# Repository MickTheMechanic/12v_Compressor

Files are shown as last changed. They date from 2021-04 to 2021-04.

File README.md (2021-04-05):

# 12v_Compressor

## An open-source Arduino controlled 12v mobile compressor using 3d printed and upcycled parts.

<br />This work is licensed under a <a rel="license" href="http://creativecommons.org/licenses/by-nc/4.0/">Creative Commons Attribution-NonCommercial 4.0 International License</a>.
#

[vid](https://youtube.com/playlist?list=PLsk74wXEuKOpL2YGHRVS3v7fIHzCto8o0)

#

## Overview

The compressor is made up of a used BMW air suspension compressor (manufacturer is WABCO, the same part is also used be Mercedes), some empty 0.95l oxygen tanks (those used for small oxy-acetylene torches), an arduino, and diverse electrical components.

The compressor is controlled via an Arduino Uno, which switches a relay on or off depending on the pressure inside the tanks. The current pressure is displayed on a 2.8" TFT screen. A small lithium battery is included, so that a pressure read out can be achieved without 12v power supply.

- If 12v supply is not present, the power button can be pressed and the display will show a realtime pressure readout for 20 seconds and switch off automatically.
- If 12v supply is present and device is switched off the lithium battery will be recharged
- If 12v supply is present and device is switchen on, the compressor will be powered on and off via the relay automatically depending on realtime pressure. The lithium battery will also be recharged. Realtime pressure will be displayed on screen.

### There are also two status LED's
#### Left LED:
- Red = lithium battery is recharging
- Blue = Lithium battery is fully charged
#### Right LED:
- Green = Tanks are full (if 12v is present relay = off)
- Red = Tanks should be refilled (if 12v is present relay = on)

#
<a href="https://ibb.co/Dz1jNbD">C740-E988-A85-A-4125-8306-F7122-EC01628</a>
#
<a href="https://ibb.co/rd78Jnq">0-F9-DC07-B-1-AC6-40-D4-9-CB7-EE59770-C8-E80</a>
#

#

#

### Extra info

This project relies on a modified version of the GUISlice library. This has been included in the repo

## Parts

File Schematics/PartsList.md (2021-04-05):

1x Arduino Uno
#
1x 2.8" lcd tft display shield
#
1x AO3401 P-channel MOSFET
#
1x IRF9640 (or similar) P-channel MOSFET
#
3x 1N5819 (or similar) diode
#
1x 1N4007 (or similar) diode
#
3x 2N2222A (or similar) NPN transistor
#
3x 470 ohm resistor
#
1x 220 ohm resistor
#
1x 10 kohm resiostor
#
1x 1A MINI fuse
#
1x Mini buck converter
#
1x 5v step up converter
#
1x TP4056 lithium battery charger module
#
1x 12v relay with built in fuse (30A)
#
2x Bi-Color LED (Common Annode!)

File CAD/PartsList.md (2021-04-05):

8x M6 x 25mm cylindrical head allen key bolts
#
8x M6 SW10 nuts
#
4x M5 x 25mm countersunk allen key bolts
#
3x M10x1 brake pipe T joiners
#
2x m10x1 male to male brake pipe joiners
#
1x 300 PSI 5v pressure transducer (1/8 NPT)
#
2x m10x1 6mm push connect fittings
#
1x 1/8 NPT to 1/4 NPT male to male adaptor
#
1x AF2000-02 air dryer
#
1x Automotive breather air filter
#
3x M6 rubber mount

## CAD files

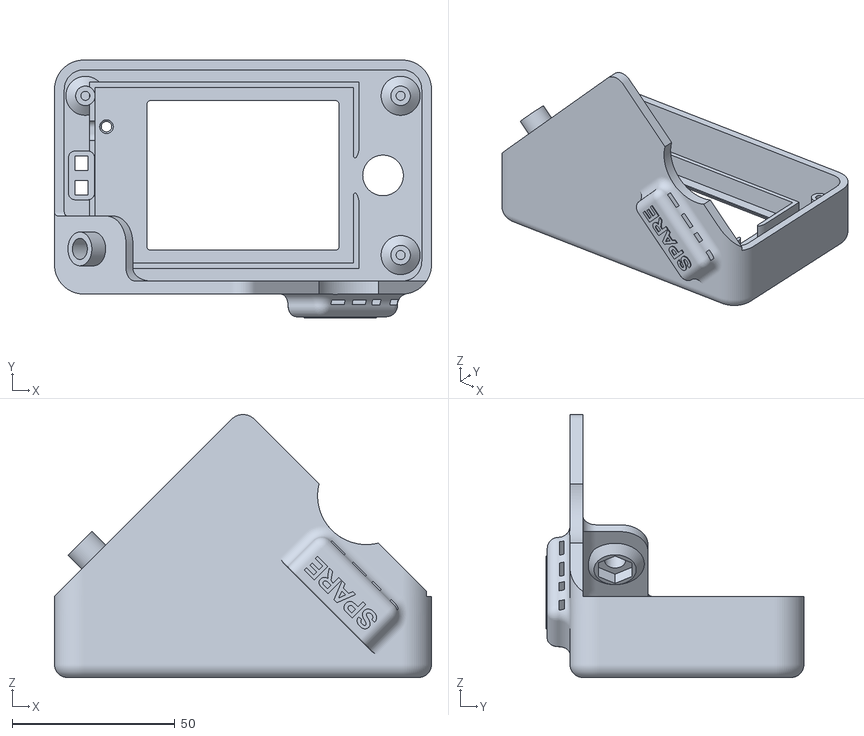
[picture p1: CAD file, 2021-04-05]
CAD/Comp. screen frontV3.stl
116.0 x 79.3 x 80.9

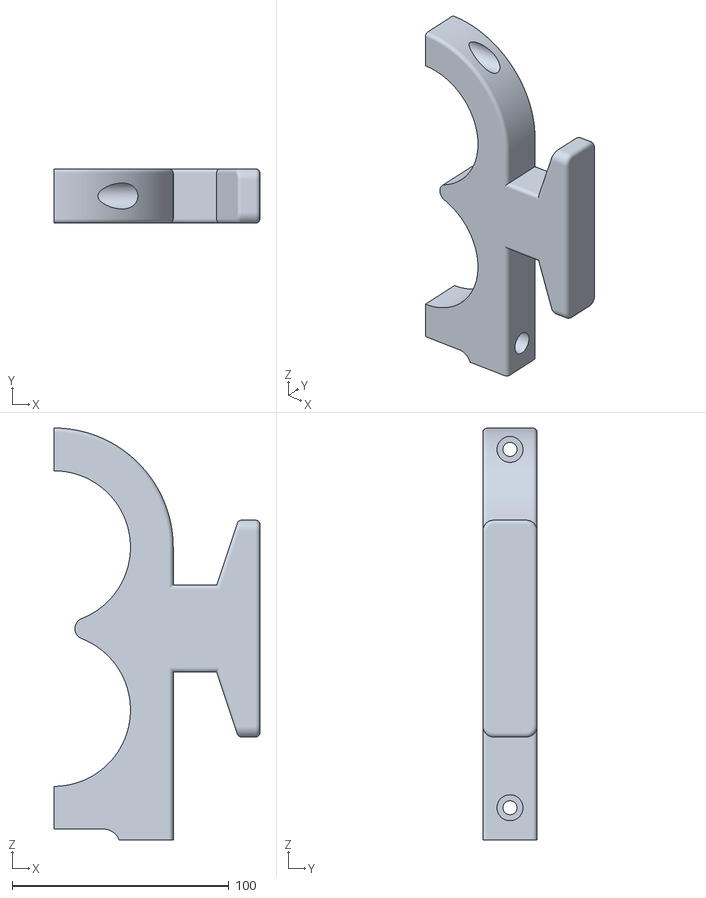
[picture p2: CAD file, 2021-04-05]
CAD/Clamp.stl
95.0 x 25.0 x 190.0

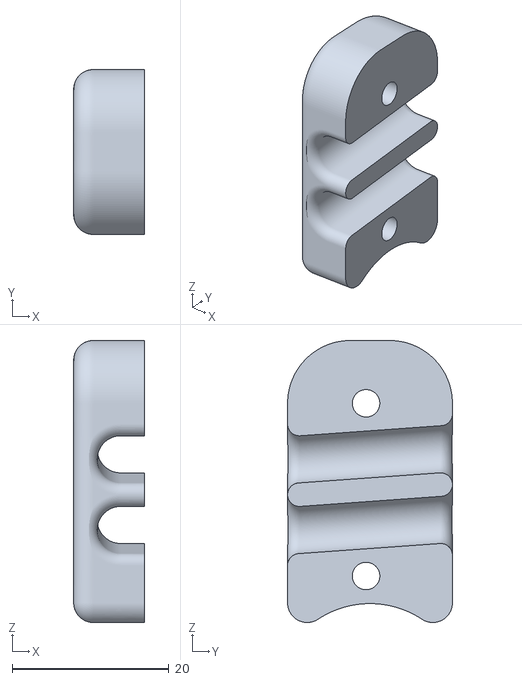
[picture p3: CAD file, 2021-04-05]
CAD/Cable clamp.stl
9.00 x 21.0 x 35.9

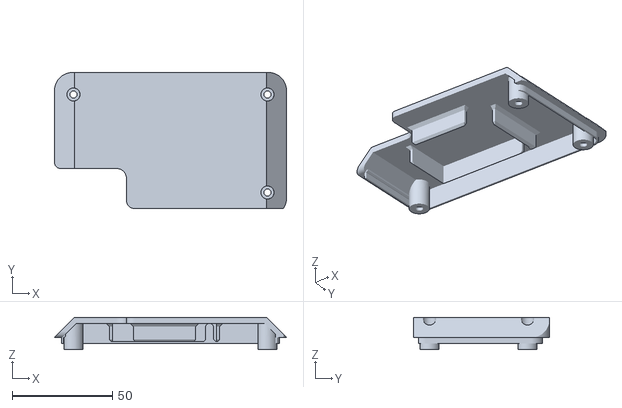
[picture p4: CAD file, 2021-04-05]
CAD/Comp. screen rearV3.stl
116.0 x 68.0 x 16.0

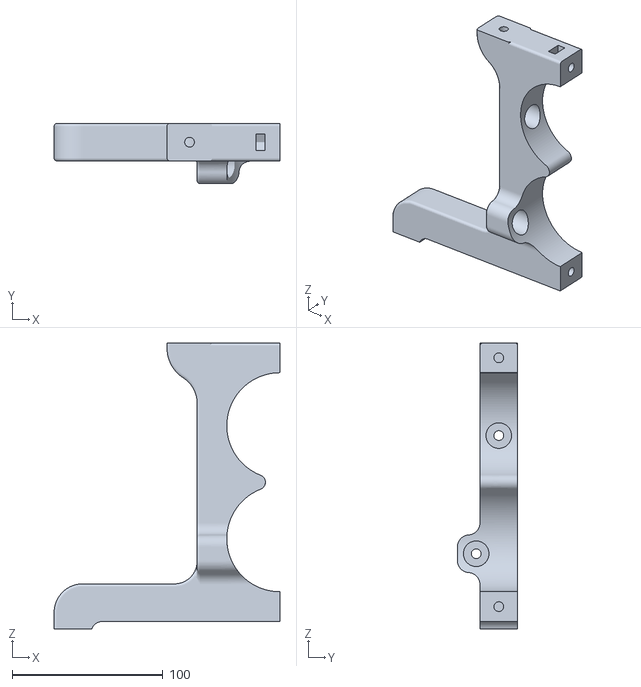
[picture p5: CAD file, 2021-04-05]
CAD/Holder 2.stl
150.0 x 40.0 x 190.0

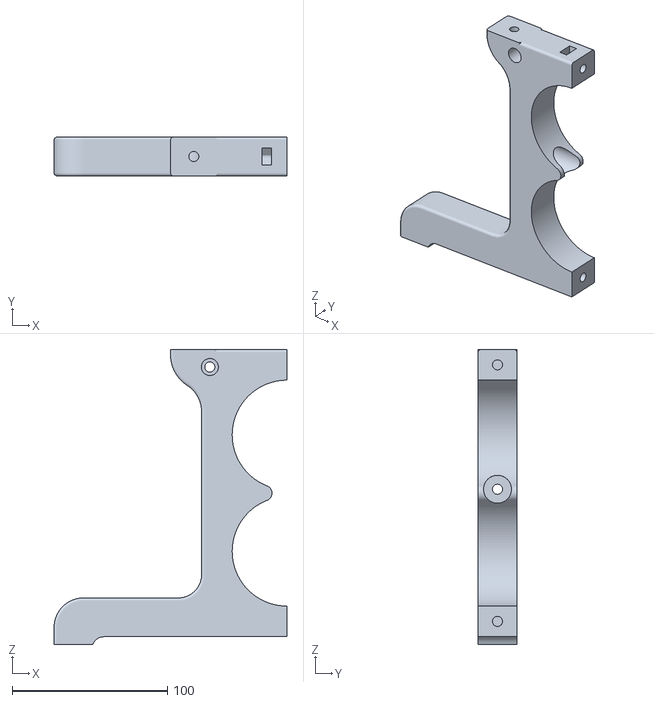
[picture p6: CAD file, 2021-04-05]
CAD/Holder 1.stl
150.0 x 25.0 x 190.0

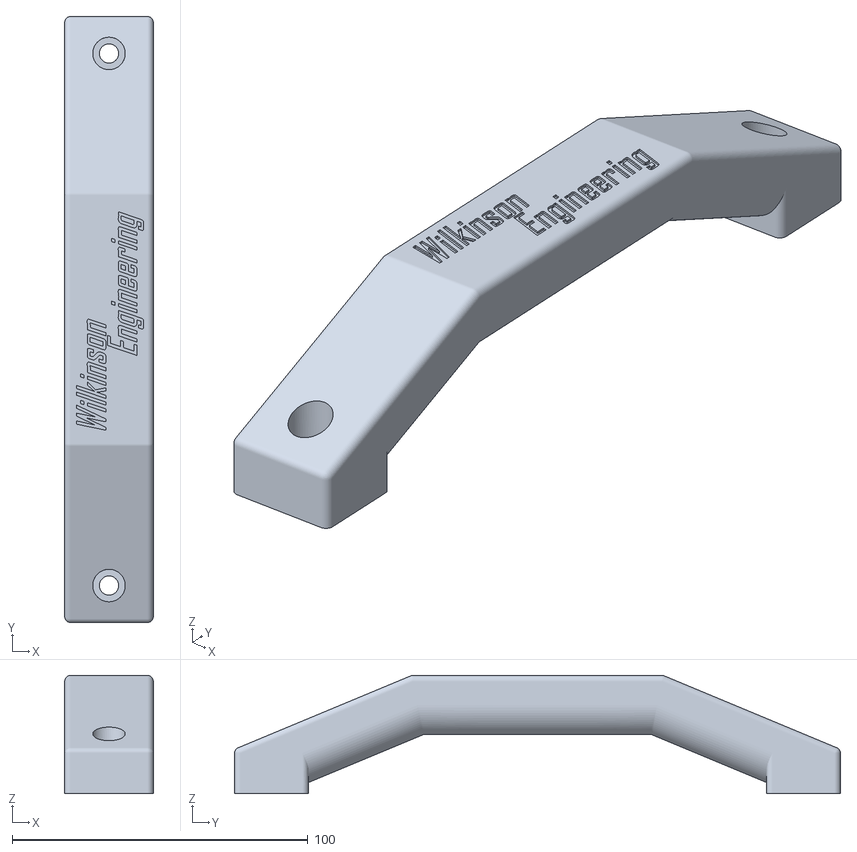
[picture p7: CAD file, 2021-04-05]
CAD/Handle.stl
30.0 x 205.0 x 40.0

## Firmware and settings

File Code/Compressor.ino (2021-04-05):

//Another ridiculously good mod by Mick ;)

#include "GUIslice.h"
#include "GUIslice_drv.h"

// Include any extended elements
#include "elem/XRingGauge.h"

// Defines for resources
#define relayPin 13        //Will turn relay on and off
#define pressurePin A5      //Connected to pressure transducer
#define latchPin  11       //Connected to latch circuit for auto shutdown if display is powered from LiPo and not from 12v
#define buckPin 10


//counting cycles as a makeshift timer. millis and unsigned longs use too much memory.
uint8_t loopcount = 0;


// Enumerations for pages, elements, fonts, images
enum { E_PG_MAIN };
enum { E_ELEM_XRING, E_ELEM_TEXT3, 
E_ELEM_TEXT2,
     };
enum { E_xGaugeFont, E_TxtFont, MAX_FONT };

// Instantiate the GUI
#define MAX_PAGE            1
#define MAX_ELEM_PG_MAIN    3

gslc_tsGui                  m_gui;
gslc_tsDriver               m_drv;
gslc_tsFont                 m_asFont[MAX_FONT];
gslc_tsPage                 m_asPage[MAX_PAGE];
gslc_tsElem                 m_asPageElem[MAX_ELEM_PG_MAIN];
gslc_tsElemRef              m_asPageElemRef[MAX_ELEM_PG_MAIN];

gslc_tsXRingGauge           m_sXRingGauge;

// Save some element references for quick access
gslc_tsElemRef*  m_pElemXRingGauge = NULL;
gslc_tsElemRef*  m_pE_ELEM_TEXT2 = NULL;

void setup()
{
  //Set pin defaults
  pinMode(pressurePin, INPUT);
  pinMode(buckPin, INPUT_PULLUP);
  pinMode(relayPin, OUTPUT);
  digitalWrite (relayPin, LOW);
  pinMode(latchPin, OUTPUT);
  digitalWrite (latchPin, HIGH); //set latchpin high to trigger latch transistor so device remains powered.

  
  gslc_tsElemRef* pElemRef = NULL;
  // Initialize
  if (!gslc_Init(&m_gui, &m_drv, m_asPage, MAX_PAGE, m_asFont, MAX_FONT)) {
    return;
  }

  // Load Fonts
  if (!gslc_FontSet(&m_gui, E_xGaugeFont, GSLC_FONTREF_PTR, NULL, 5)) {
    return;
  }
  if (!gslc_FontSet(&m_gui, E_TxtFont, GSLC_FONTREF_PTR, NULL, 3)) {
    return;
  }

  // -----------------------------------

  // Create page elements
  gslc_PageAdd(&m_gui, E_PG_MAIN, m_asPageElem, MAX_ELEM_PG_MAIN, m_asPageElemRef, MAX_ELEM_PG_MAIN);

  // Background flat color
  gslc_SetBkgndColor(&m_gui, GSLC_COL_BLACK);


  // Create a RingGauge
  static char m_str3[3] = "";
  pElemRef = gslc_ElemXRingGaugeCreate(&m_gui, E_ELEM_XRING, E_PG_MAIN, &m_sXRingGauge,
  (gslc_tsRect) {
    15, 50, 210, 210
  }, m_str3, 3, E_xGaugeFont);
  gslc_ElemXRingGaugeSetValRange(&m_gui, pElemRef, 0, 15);
  gslc_ElemXRingGaugeSetVal(&m_gui, pElemRef, 45); // Set initial value
  gslc_ElemXRingGaugeSetAngleRange(&m_gui, pElemRef, -135, 270, true); // Three-Quarter circle
  gslc_ElemXRingGaugeSetThickness(&m_gui, pElemRef, 35);
  gslc_ElemXRingGaugeSetColorInactive(&m_gui, pElemRef, GSLC_COL_GRAY_DK2);
  gslc_ElemXRingGaugeSetColorActiveGradient(&m_gui, pElemRef, GSLC_COL_ORANGE, GSLC_COL_GREEN);
  gslc_ElemSetTxtCol  ( &m_gui, pElemRef, GSLC_COL_WHITE ) ;
  m_pElemXRingGauge = pElemRef; // Save for quick access


  //Create text "BAR"
  pElemRef = gslc_ElemCreateTxt(&m_gui, E_ELEM_TEXT3, E_PG_MAIN, (gslc_tsRect) {
    81, 250, 73, 34
  },
  (char*)"BAR", 0, E_xGaugeFont);
  gslc_ElemSetTxtCol(&m_gui, pElemRef, ((gslc_tsColor) {
    245, 246, 250
  }));


  //Create text "REFILL!"
  pElemRef = gslc_ElemCreateTxt(&m_gui, E_ELEM_TEXT2, E_PG_MAIN, (gslc_tsRect) {
    65, 10, 145, 34
  }, (char*)"REFILL!", 0, E_TxtFont);
  gslc_ElemSetTxtCol(&m_gui, pElemRef, GSLC_COL_ORANGE);
  gslc_ElemSetVisible  ( &m_gui, pElemRef, false);
  m_pE_ELEM_TEXT2 = pElemRef; // Save for quick access



  // -----------------------------------
  // Start up display on main page
  gslc_SetPageCur(&m_gui, E_PG_MAIN);

}





void loop()
{
  char acStr[3];
  delay (200);
  

  //Map transducer to bar: 0.5v - 4.5v = 0 - 20 BAR
  //I made up some simple integer math as map() function uses too much memory
  int8_t currentPressure = ((analogRead(pressurePin)-102)/41);

  //set min and max pressures
  //I include these in the loop so that they are placed in dynamic memory. there is too little space in progmem.
 uint8_t offPressure = 16;
 uint8_t onPressure = 12;

  //turn on relay if pressure drops below 12 bar
  if (currentPressure <= onPressure) {
    digitalWrite(relayPin, HIGH);  
    //Show "REFILL!" text
    gslc_ElemSetVisible  ( &m_gui, m_pE_ELEM_TEXT2, true);
  }
  //turn off relay when pressure reaches 15 bar
  else if (currentPressure >= offPressure) {
    digitalWrite(relayPin, LOW);
    //Hide "REFILL!" text
    gslc_ElemSetVisible  ( &m_gui, m_pE_ELEM_TEXT2, false);
  }

  //auto shutdown timer. Only runs if buckPin is high (ie. only runs if there is no 12v supply).
  //Counting loop cycles as a makeshift timer. millis and unsigned longs use too much memory.
  if (digitalRead (buckPin) == HIGH) {
    loopcount ++;
    if (loopcount == 80) {
      digitalWrite (latchPin, LOW);
    }
  }

  //Set pressure value to ring gauge
  gslc_ElemXRingGaugeSetVal(&m_gui, m_pElemXRingGauge, (currentPressure));

  //Print pressure on screen
  sprintf(acStr, "%d", currentPressure);
  gslc_ElemSetTxtStr(&m_gui, m_pElemXRingGauge, acStr);

// Periodically call GUIslice update function
  gslc_Update(&m_gui);
  
}
